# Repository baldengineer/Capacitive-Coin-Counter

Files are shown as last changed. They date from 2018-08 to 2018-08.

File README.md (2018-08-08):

## Capacitive Coin Counter
Project for a video to make use of an automatic coin detector. It can be programmed to identify up to 4 coins.

### Code
Code for the Arduino and MSP430

### Electronics
Schematics for the 12V boost regulator and the breadboard

### Enclosure
Laser cut and 3d printing files to build the box.

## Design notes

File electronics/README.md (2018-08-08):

Electronics for my Capacitive Coin Counter.

In addition to these, you'll also need an OLED Screen, a Coin Accepter from Adafruit (adafruit coin acceptor), PowerBoost 500 or 1000 (https://www.element14.com/community/docs/DOC-89078/l/power-boost-1000-charger-board) from Adafruit, and a MSP430FR2633 (https://www.element14.com/community/docs/DOC-81128/l/capacitive-touch-evaluation-and-rapid-prototyping-for-msp430fr2633-microcontroller-mcu-development-kit) or MSP430 board from a CAPTIVATE Design Kit.

Oh and an Arduino. I used the Pyramiduino (https://www.hackster.io/baldengineer/pyramiduino-6d42c7), a board I designed to teach PCB design.

12V Boost > A 2.5V to 12 or 24V boost converter. Suitable for 50mA operation.
Breadboard > Various circuits to support the project build.

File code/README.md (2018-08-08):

arduino> contains all of the code to control the coin acceptor and oled. Bank's value is stored in the Arduino's EEPROM.

MSP430> Contains the code for a MSP430FR2633 development board. It turns on the PowerBoost which turns on the Arduino. It uses capacitive sensing to turn-on and for the "reset bank" signal. It wakes up every 100ms to check for a touch. It keeps the arduino on for 10-12 seconds after it detects the last proximity.

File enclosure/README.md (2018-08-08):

laser cut pieces > the main box and draw cut using 3mm acrylic.
3d printed pieces > the slides for the drawer

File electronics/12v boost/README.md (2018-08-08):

A ~3V to 12V or 24V boost converter. The resistors listed in the BOM are for 12V. Change the R3 to 56K to get 24V out. Regulator can handle about 50 mA continous and peaks up to 500 mA. Based on the Microchip MCP1661. You can order the board from OSHPark: https://oshpark.com/shared_projects/hU1dj3Ux

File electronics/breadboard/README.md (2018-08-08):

These circuits are built on an Adafruit perma Protoboard. 

https://www.adafruit.com/product/1609

Great protoboards, very high quality. Circuits easily move from breadboard to it. (Exactly what I did.)

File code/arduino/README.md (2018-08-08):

You will need to install the U8G2 LCD library (https://github.com/olikraus/u8g2). I picked this library because it works with practically any kind of LCD screen. In my case, I'm using a generic OLED with I2C and no reset signal.

This code is intended for the 8-bit Arduino like an Uno or Nano.

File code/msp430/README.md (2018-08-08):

You'll need TI's CAPTIVATE Design Center and Code Composer Studio.

1. Create a panel design in Design Studio with a single button, proximity detect, and the MSP430FR2633. 
2. In Design Center, Auto-Configure the pins, but then change the button to use CAP2.0 and CAP0.0.
3. Export this project to code composer studio
4. Import in Code Composer Studio (you can't just open it)
5. Replace main.c with this one.
6. Copy CAPT_UserConfig.c and CAPT_UserConfig.h to captivate_config

I NEVER got the "update existing project" to work in Design Center. So any changes you make there, make in the CAPT_UserConfig.h file.

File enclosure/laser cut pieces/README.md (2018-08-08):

Everything was cut on 1/8" acrylic, but was designed for 3mm.

Main > Contains all of the otter box pieces, including the panel cover for the drawer. The cents symbol can be engraved, painted, or ommitted. I glued the pieces together with super glue. 

Drawer > Contains all of the drawer pieces. 

Rails > These rails glue to the drawer.

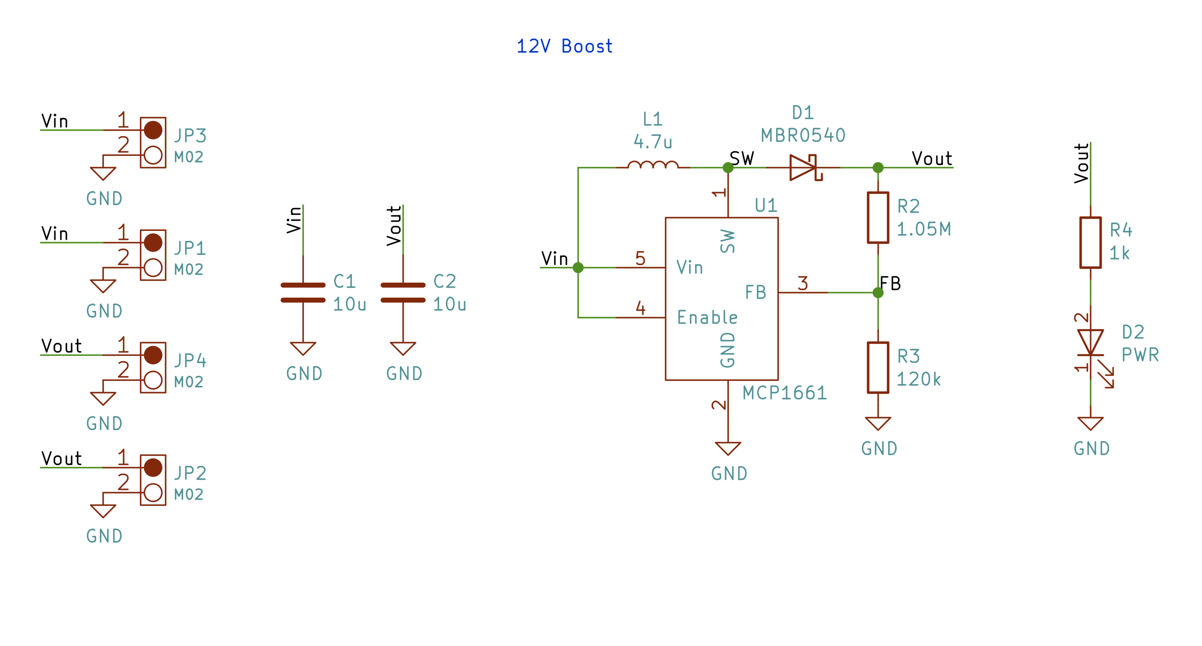
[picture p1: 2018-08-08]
electronics/12v boost/12V Boost Converter Schematic.png

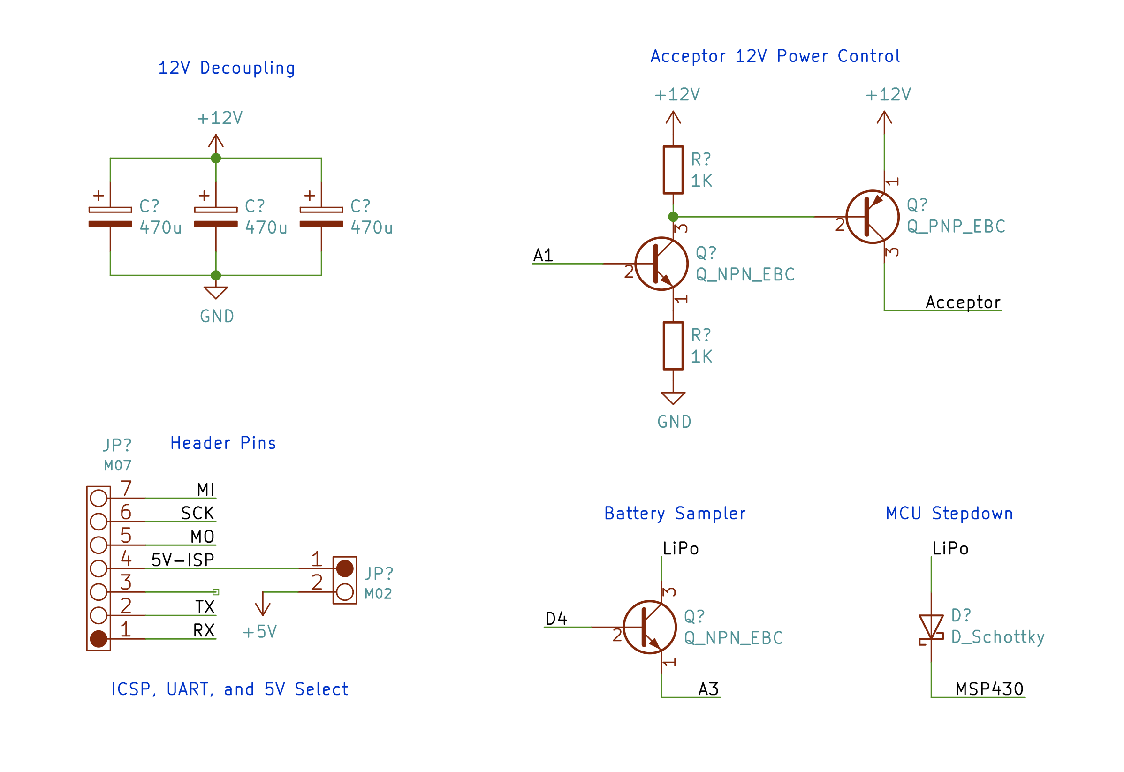
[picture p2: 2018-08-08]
electronics/breadboard/Breadboard Circuits.png

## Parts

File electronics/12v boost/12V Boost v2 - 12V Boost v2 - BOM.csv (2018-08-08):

Ref | Qnty | Value | Cmp name | Description | Vendor
C1, C2, | 2 | 10u | C | Unpolarized capacitor
D1, | 1 | MBR0540 | D_Schottky | Schottky diode
D2, | 1 | PWR | LED | LED generic
L1, | 1 | 4.7u | L | Inductor
R2, | 1 | 1.05M | R | Resistor
R3, | 1 | 120k | R | Resistor
R4, | 1 | 1k | R | Resistor
U1, | 1 | MCP1661 | MCP1661

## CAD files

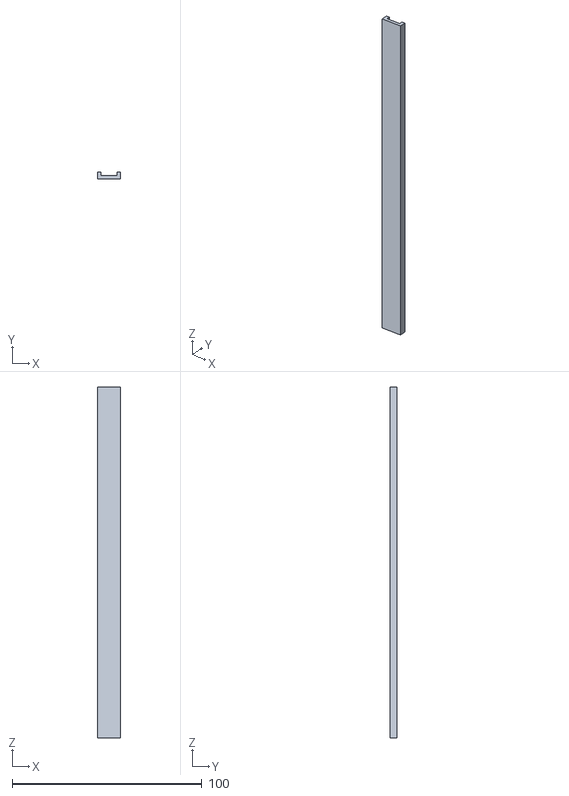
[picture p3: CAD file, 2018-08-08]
enclosure/3d printed pieces/side slider mk4 (185mm) v3.stl
12.0 x 3.75 x 185.0

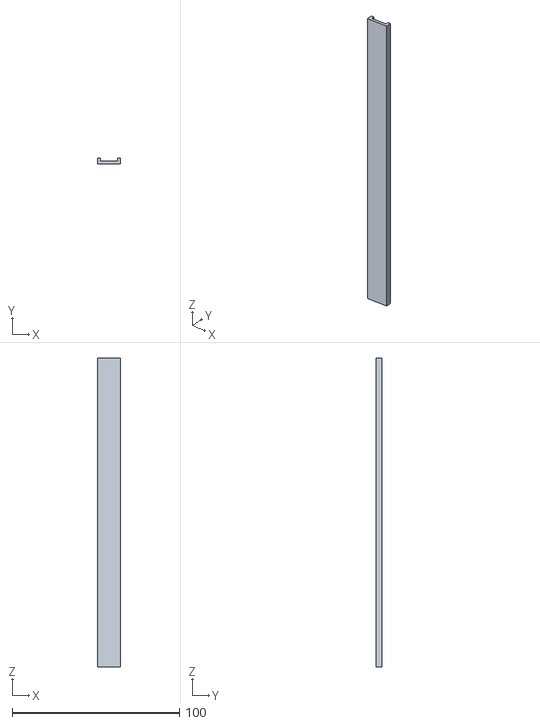
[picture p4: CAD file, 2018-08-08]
enclosure/3d printed pieces/Bottom Slider mk4 (185mm) v5.stl
14.0 x 3.75 x 185.0

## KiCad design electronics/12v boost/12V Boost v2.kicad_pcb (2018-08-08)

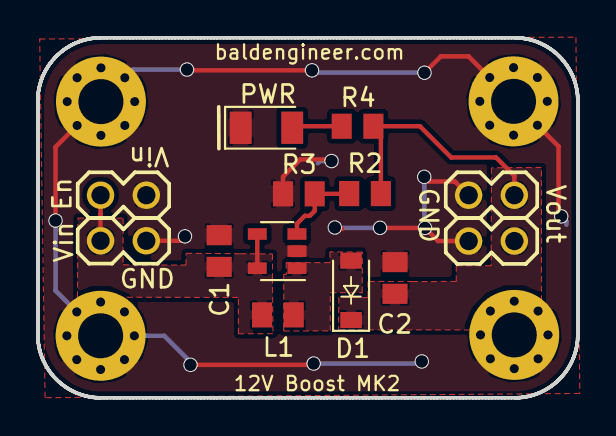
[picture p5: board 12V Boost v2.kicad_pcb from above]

Board: 2 copper layers, 30.0 x 20.0 mm, 17 parts (0 on the bottom side), 6 nets.

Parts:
C1, C2: 10u; C_0805_2012Metric
D1: MBR0540; D_SOD-123
D2: PWR; LED_1206_3216Metric
JP1, JP2, JP3, JP4: M02; 1X02
L1: 4.7u; L_0805_2012Metric
MK1, MK2, MK3, MK4: Mounting_Hole_PAD; MountingHole_2.5mm_Pad_Via
R2: 1.05M; R_0805_2012Metric
R3: 120k; R_0805_2012Metric
R4: 1k; R_0805_2012Metric
U1: MCP1661; SOT-23-5

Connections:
/FB: R2.2, R3.1, U1.3
/SW: D1.2, L1.2, U1.1
/Vin: C1.1, JP1.1, JP3.1, L1.1, U1.4, U1.5
/Vout: C2.1, D1.1, JP2.1, JP4.1, R2.1, R4.2
GND: C1.2, C2.2, D2.1, JP1.2, JP2.2, JP3.2, JP4.2, MK1.1, MK2.1, MK3.1, MK4.1, R3.2, U1.2
unnamed: D2.2, R4.1

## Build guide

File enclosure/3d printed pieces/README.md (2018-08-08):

You need two of each of these slides. The Bottom are slightly wider to be more forgiving, especially as the draw gets heavier.

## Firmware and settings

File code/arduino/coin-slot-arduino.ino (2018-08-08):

#include <Arduino.h>
#include <EEPROM.h>
#include <Wire.h>
#include <U8g2lib.h>
#include "coin-slot-arduino.h"


// u8g2 constructor
U8G2_SSD1306_128X64_NONAME_F_HW_I2C u8g2(U8G2_R2, /* reset=*/ U8X8_PIN_NONE);

void loadEEPROM() {
	EEPROM.get(0, bankCount);
	EEPROMbankCount = bankCount;
}

byte getValueWidth(float displayValue) {
  // average character width for u8g2_font_logisoso24_tn is 14
  const byte charWidth = u8g2.getMaxCharWidth();
  byte theWidth = 4 * charWidth; //1.00
  if (displayValue >= 10.00)
    theWidth = 5 * charWidth;
  if (displayValue >= 100.00)
    theWidth = 6 * charWidth; //1.00
  if (displayValue >= 1000.00)
    theWidth = 7 * charWidth; //1.00
return ((u8g2.getDisplayWidth()-theWidth)/2);
}


void printOLED() {
	u8g2.clearBuffer();					    // clear the internal memory
	u8g2.setFont(u8g2_font_logisoso34_tn);	// choose a suitable font
	byte centerHeight = (u8g2.getDisplayHeight()/2) + (u8g2.getMaxCharHeight()/2);
	u8g2.setCursor(getValueWidth(bankValue),centerHeight);
	u8g2.print(bankValue);
	u8g2.sendBuffer();					    // transfer internal memory to the display
}

void printBank() {
	bankValue = bankCount * coinValue;
	printOLED();
	Serial.print(F("Bank Value: "));
	Serial.println(bankValue);
}

void printPulses() {
	Serial.print(F("Pulse coutn: "));
	Serial.println(bankCount);
}


void handleSerial() {
	char incomingChar = Serial.read();

	switch(incomingChar) {
		case '!':
			Serial.println(F("Clearing..."));
			bankCount = 0;
      bankValue = bankCount * coinValue;
      printBank();
      break;
    case '.':
      printPulses();
      printBank();
      break;
	}
}

void checkBattery() {

	// hceck battery voltage
	digitalWrite(battControl, HIGH);
	delay(10);
	int battReading = analogRead(battRead);
	digitalWrite(battControl, LOW);
//	Serial.print(F("Battery: "));
//	Serial.println(battReading);
	if (battReading < 700) {
		// battery is too low, turn off solenoid
		enableCounter = false;
		// turn off enableCounter
		digitalWrite(hvSolenoid, LOW);
		//print message
//		Serial.println(F("Low Battery Disable"));
		u8g2.clearBuffer();					// clear the internal memory
		u8g2.setFont(u8g2_font_logisoso34_tr);	// choose a suitable font
		u8g2.drawStr(0, 50, "lo batt");
		u8g2.sendBuffer();					// transfer internal memory to the display
		while(1);
	}

	return;
}

void handleBankReset() {
	unsigned long resetCounter = millis();
	bool waiting = true;
	while((digitalRead(resetButton) == HIGH) && waiting) {
		if (millis() - resetCounter < 1000) {
			u8g2.clearBuffer();					// clear the internal memory
			u8g2.setFont(u8g2_font_logisoso34_tr);	// choose a suitable font
			u8g2.drawStr(0, 50, "3");
			u8g2.sendBuffer();					// transfer internal memory to the display
		}

		if ((millis() - resetCounter > 1000) && (millis() - resetCounter <= 2000)) {
			u8g2.clearBuffer();					// clear the internal memory
			u8g2.setFont(u8g2_font_logisoso34_tr);	// choose a suitable font
			u8g2.drawStr(0, 50, "2");
			u8g2.sendBuffer();					// transfer internal memory to the display
		}

		if ((millis() - resetCounter > 2000) && (millis() - resetCounter <= 3000)) {
			u8g2.clearBuffer();					// clear the internal memory
			u8g2.setFont(u8g2_font_logisoso34_tr);	// choose a suitable font
			u8g2.drawStr(0, 50, "1");
			u8g2.sendBuffer();					// transfer internal memory to the display
		}

		if ((millis() - resetCounter > 3000) && (millis() - resetCounter <= 3500)) {
			u8g2.clearBuffer();					// clear the internal memory
			u8g2.setFont(u8g2_font_logisoso34_tr);	// choose a suitable font
			u8g2.drawStr(0, 50, "0");
			u8g2.sendBuffer();					// transfer internal memory to the display
		}

		if ((millis() - resetCounter > 3500) && (millis() - resetCounter <= 4000)) {
			bankCount = 0;
		}

		if ((millis() - resetCounter > 4000)) {
			waiting = false;
		}

	}
	printBank();
}

void setup() {
	pinMode(battControl, OUTPUT);   // battery transistor
	digitalWrite(battControl, LOW);
	u8g2.begin();
	checkBattery();
	// init coin counter
	pinMode(hvSolenoid, OUTPUT);
	//Serial.print(F("Turning on counter..."));
  digitalWrite(hvSolenoid, HIGH);
	pinMode(coinSig, INPUT_PULLUP);
	u8g2.clearBuffer();					// clear the internal memory
	u8g2.setFont(u8g2_font_logisoso34_tr);	// choose a suitable font
	u8g2.drawStr(0, 50, "Wait");
	u8g2.sendBuffer();					// transfer internal memory to the display
	Serial.begin(115200);
  //delay(100); // TODO is there a way to tell when coin acceptor is ready
  while(digitalRead(coinSig));  // add timeout and error.
	previousCoinSignal = digitalRead(coinSig);
  //Serial.println(F("done!"));

	pinMode(resetButton, INPUT);

  // init screen
  //pinMode(hvOLED, OUTPUT);
	loadEEPROM();
	//Serial.print(F("After Setup: "));
	//Serial.println(freeMemory());
	printBank();
}

void loop() {
	handleSerial();

	if (digitalRead(resetButton) == HIGH)
		handleBankReset();

	if (millis() - previousBatteryMillis >= batteryInterval) {
		previousBatteryMillis = millis();
		checkBattery();
	}


	byte currentCoinSignal = digitalRead(coinSig);

	if (currentCoinSignal == HIGH) {
		previousUpdateMillis = millis(); // print after pulse train is done
    previousEEPROMwrite = millis(); // don't write until pulse train is over
		printOnceFlag = true;
	}

  // only print after pulses stop
	if (printOnceFlag && (millis() - previousUpdateMillis >= updateInterval)) {
		printBank();
		printOnceFlag = false;
	}

	// is time to update the EEPROM?

	if (millis() - previousEEPROMwrite >= updateEEPROMinterval) {
		// reset the clock
		previousEEPROMwrite = millis();

		// only write to EEPROM when a new value
		if (bankCount != EEPROMbankCount) {
			EEPROM.put(0,bankCount);  // writes a float to EEPROM
			Serial.println(F("!!! EEPROM WRITE !!!"));
			EEPROMbankCount = bankCount;
		}
	}

	if (currentCoinSignal != previousCoinSignal) {
		// Save the state for next iteration
		previousCoinSignal = currentCoinSignal;

		if (currentCoinSignal == HIGH) {
      // we see an edge, but is it a coin pulse?
      armedForCount = millis();
		} else {
      // short timeout to make sure it was a full pulse
      if (millis() - armedForCount < pulseTimeOut) {
        bankCount++;
      }
    }
	}
}

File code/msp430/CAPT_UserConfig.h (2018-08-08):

/* --COPYRIGHT--,BSD
 * Copyright (c) 2017, Texas Instruments Incorporated
 * All rights reserved.
 *
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
 * *  Redistributions of source code must retain the above copyright
 *    notice, this list of conditions and the following disclaimer.
 *
 * *  Redistributions in binary form must reproduce the above copyright
 *    notice, this list of conditions and the following disclaimer in the
 *    documentation and/or other materials provided with the distribution.
 *
 * *  Neither the name of Texas Instruments Incorporated nor the names of
 *    its contributors may be used to endorse or promote products derived
 *    from this software without specific prior written permission.
 *
 * THIS SOFTWARE IS PROVIDED BY THE COPYRIGHT HOLDERS AND CONTRIBUTORS "AS IS"
 * AND ANY EXPRESS OR IMPLIED WARRANTIES, INCLUDING, BUT NOT LIMITED TO,
 * THE IMPLIED WARRANTIES OF MERCHANTABILITY AND FITNESS FOR A PARTICULAR
 * PURPOSE ARE DISCLAIMED. IN NO EVENT SHALL THE COPYRIGHT OWNER OR
 * CONTRIBUTORS BE LIABLE FOR ANY DIRECT, INDIRECT, INCIDENTAL, SPECIAL,
 * EXEMPLARY, OR CONSEQUENTIAL DAMAGES (INCLUDING, BUT NOT LIMITED TO,
 * PROCUREMENT OF SUBSTITUTE GOODS OR SERVICES; LOSS OF USE, DATA, OR PROFITS;
 * OR BUSINESS INTERRUPTION) HOWEVER CAUSED AND ON ANY THEORY OF LIABILITY,
 * WHETHER IN CONTRACT, STRICT LIABILITY, OR TORT (INCLUDING NEGLIGENCE OR
 * OTHERWISE) ARISING IN ANY WAY OUT OF THE USE OF THIS SOFTWARE,
 * EVEN IF ADVISED OF THE POSSIBILITY OF SUCH DAMAGE.
 * --/COPYRIGHT--*/


// Generated by Captivate Design Center v1_60_00_00 on Thu Aug 02 07:45:00 PDT 2018


//*****************************************************************************
// CAPT_UserConfig.h
//
//! The Captivate touch library UserConfig component defines the architecture
//! of the capacitive touch panel that is being implemented.
//
//! \version 1.60.00.03
//! Released on November 22, 2017
//
//*****************************************************************************

//*****************************************************************************
//
// NOTE: This is an automatically generated source code file!  The Captivate
// Design Center generates the User Configuration file automatically based
// upon the sensor layout that was created.
//
// Changes to this file will be OVERWRITTEN if a you select
// "Update Existing Project" under "Generate Source Code" in the Design Center.
//
// To avoid interference with the code generation process, keep ALL application
// code external to this file.
//
//*****************************************************************************

#ifndef CAPT_USERCONFIG_H_
#define CAPT_USERCONFIG_H_

//
// CapTIvate User Configuration Template Version
//
#ifndef __CAPTIVATE_CONFIG_VERSION__
#define __CAPTIVATE_CONFIG_VERSION__ 16000
#endif

//
// Include the CapTIvate Software Library
//
#include "captivate.h"

//
// Compile-Time System Configuration Definitions
//
#define CAPT_SENSOR_COUNT                     (2)
#define CAPT_INTERFACE  (__CAPT_BULKI2C_INTERFACE__)
#define CAPT_CONDUCTED_NOISE_IMMUNITY_ENABLE  (false)
#define CAPT_WAKEONPROX_ENABLE  (true)
#define CAPT_WAKEONPROX_SENSOR  (PRX00)
#define CAPT_TRACKPAD_ENABLE  (false)
#define CAPT_GESTURE_ENABLE  (false)
#define CAPT_CAL_ALG  (__CAPT_STD_CALIBRATION__)

//
// Captivate Frequency Count Definitions
// If conducted noise is enabled, multiple
// frequency scanning is enabled.  These definitions
// ensure that RAM space is set aside to store
// frequency specific information.
//
#if CAPT_CONDUCTED_NOISE_IMMUNITY_ENABLE
#define CAPT_SELF_FREQ_CNT        (4)
#define CAPT_MUTUAL_FREQ_CNT      (4)
#else
#define CAPT_SELF_FREQ_CNT        (1)
#define CAPT_MUTUAL_FREQ_CNT      (1)
#endif

//*****************************************************************************
//
//! \def CAPT_MS_TO_CYCLES is a macro to convert a period value in 
//! milliseconds to an approximate cycle count based on a 
//! 32.768 kHz clock frequency.
//
//*****************************************************************************
#define CAPT_MS_TO_CYCLES(ms)                                         (ms * 32)

//*****************************************************************************
//
//! \def CAPT_MS_TO_CYCLES_VLO is a macro to convert a period value in
//! milliseconds to an approximate cycle count based on a
//! 10 kHz clock frequency.  The VLO oscillator is approximately 10 kHz.
//
//*****************************************************************************
#define CAPT_MS_TO_CYCLES_VLO(ms)                                     (ms * 10)

//
// Captivate Sensor Prototypes
// These prototypes enable access to sensors
// from the application.
//
extern tSensor BTN00;
extern tSensor PRX00;
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

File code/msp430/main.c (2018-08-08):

/* --COPYRIGHT--,BSD
 * Copyright (c) 2017, Texas Instruments Incorporated
 * All rights reserved.
 *
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
 * *  Redistributions of source code must retain the above copyright
 *    notice, this list of conditions and the following disclaimer.
 *
 * *  Redistributions in binary form must reproduce the above copyright
 *    notice, this list of conditions and the following disclaimer in the
 *    documentation and/or other materials provided with the distribution.
 *
 * *  Neither the name of Texas Instruments Incorporated nor the names of
 *    its contributors may be used to endorse or promote products derived
 *    from this software without specific prior written permission.
 *
 * THIS SOFTWARE IS PROVIDED BY THE COPYRIGHT HOLDERS AND CONTRIBUTORS "AS IS"
 * AND ANY EXPRESS OR IMPLIED WARRANTIES, INCLUDING, BUT NOT LIMITED TO,
 * THE IMPLIED WARRANTIES OF MERCHANTABILITY AND FITNESS FOR A PARTICULAR
 * PURPOSE ARE DISCLAIMED. IN NO EVENT SHALL THE COPYRIGHT OWNER OR
 * CONTRIBUTORS BE LIABLE FOR ANY DIRECT, INDIRECT, INCIDENTAL, SPECIAL,
 * EXEMPLARY, OR CONSEQUENTIAL DAMAGES (INCLUDING, BUT NOT LIMITED TO,
 * PROCUREMENT OF SUBSTITUTE GOODS OR SERVICES; LOSS OF USE, DATA, OR PROFITS;
 * OR BUSINESS INTERRUPTION) HOWEVER CAUSED AND ON ANY THEORY OF LIABILITY,
 * WHETHER IN CONTRACT, STRICT LIABILITY, OR TORT (INCLUDING NEGLIGENCE OR
 * OTHERWISE) ARISING IN ANY WAY OUT OF THE USE OF THIS SOFTWARE,
 * EVEN IF ADVISED OF THE POSSIBILITY OF SUCH DAMAGE.
 * --/COPYRIGHT--*/
//*****************************************************************************
// Development main.c for MSP430FR2633, MSP430FR2533, MSP430FR2632, and
// MSP430FR2532.
//
// This starter application initializes the CapTIvate touch library
// for the touch panel specified by CAPT_UserConfig.c/.h via a call to
// CAPT_appStart(), which initializes and calibrates all sensors in the
// application, and starts the CapTIvate interval timer.
//
// Then, the capacitive touch interface is driven by calling the CapTIvate
// application handler, CAPT_appHandler().  The application handler manages
// whether the user interface (UI) is running in full active scan mode, or
// in a low-power wake-on-proximity mode.
//
// The CapTIvate application handler will return true if proximity was
// detected on any of the sensors in the application, which is used here
// to control the state of LED2. LED1 is set while the background loop enters
// the handler, and is cleared when the background loop leaves the handler.
//
// \version 1.60.00.03
// Released on November 22, 2017
//
//*****************************************************************************

#include <msp430.h>                      // Generic MSP430 Device Include
#include "driverlib.h"                   // MSPWare Driver Library
#include "captivate.h"                   // CapTIvate Touch Software Library
#include "CAPT_App.h"                    // CapTIvate Application Code
#include "CAPT_BSP.h"                    // CapTIvate EVM Board Support Package

void main(void)
{
	//
	// Initialize the MCU
	// BSP_configureMCU() sets up the device IO and clocking
	// The global interrupt enable is set to allow peripherals
	// to wake the MCU.
	//
	WDTCTL = WDTPW | WDTHOLD;
	BSP_configureMCU();

// for the reset button
#define RESCOUNT_POUT                                                       (P1OUT)
#define RESCOUNT_PDIR                                                       (P1DIR)
#define RESCOUNT_PIN                                                         (BIT7)
#define RESCOUNT_ON                                         (RESCOUNT_POUT |= RESCOUNT_PIN)
#define RESCOUNT_OFF                                       (RESCOUNT_POUT &= ~RESCOUNT_PIN)
#define RESCOUNT_TOGGLE                                     (RESCOUNT_POUT ^= RESCOUNT_PIN)

	P1OUT &= ~BIT0;         // PowerBoost control, LOW = OFF
	P1DIR |= BIT0;


	__bis_SR_register(GIE);

	//
	// Start the CapTIvate application
	//
	CAPT_appStart();

	//
	// Background Loop
	//
	while(1)
	{
		//
		// Run the captivate application handler.
		// Set LED2 if proximity is detected
		// on any sensor.
		//
        unsigned long counter = 0;
		if(CAPT_appHandler()==true) {
            LED2_ON;
            P1OUT |= BIT0;
            while (counter < 0xFFFE) {
                counter++;
                __delay_cycles(2500);
                if(CAPT_appHandler()==true) {
                    counter = 0;
                    LED1_TOGGLE;
                }
                if (BTN00.bSensorTouch == true) {
                    RESCOUNT_ON;
                } else {
                    RESCOUNT_OFF;
                }
            }
            P1OUT &= ~BIT0;
            LED2_OFF;
		}


		
		//
		// This is a great place to add in any 
		// background application code.
		//
		__no_operation();

		//
		// End of background loop iteration
		// Go to sleep if there is nothing left to do
		//

		CAPT_appSleep();
		
	} // End background loop
} // End main()
